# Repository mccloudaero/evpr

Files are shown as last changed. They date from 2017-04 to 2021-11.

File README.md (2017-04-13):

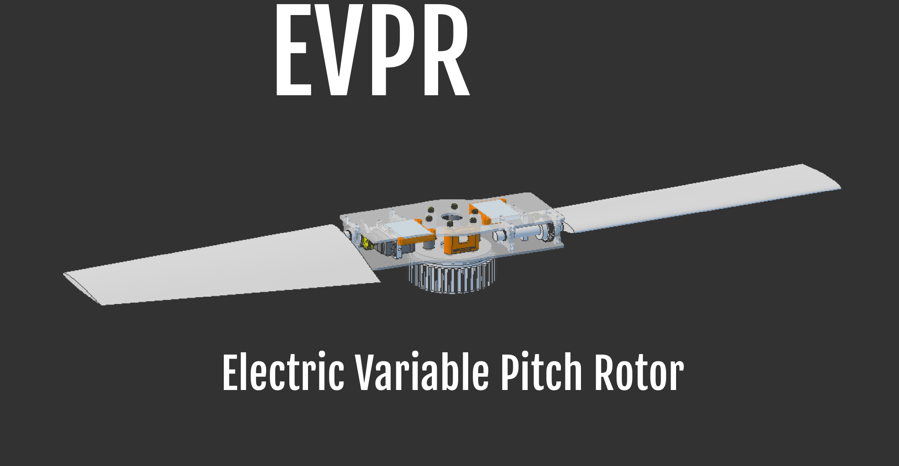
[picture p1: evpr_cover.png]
Cover

# Electric Variable Pitch Rotor (EVPR)
This repository contains the design data for the EVPR designed by
[McCloud Aero Corp](http://www.mccloudaero.com). The primary documentation source can be found at the
[Hackaday Project Page](https://hackaday.io/project/20473-evpr-electric-variable-pitch-rotor)

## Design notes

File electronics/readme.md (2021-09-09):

# Electronics
Electronics design files for EVPR project.

## Contents
* fabrication - Design files for EVPR fabrication processes, including (eventually) full SOPs for each board
* scripts - Scripts used at various points for automating mass alterations to boardfiles
* info - Various human-readable information about the project, including image versions of boardfiles and BOM
* boadfiles - The actual working boardfiles for the EVPR project.

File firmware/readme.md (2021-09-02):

## A summary of the build structure for the absolute newcommer to ESP-IDF:

Firmware for EVPR based on ESP-IDF and ESPNOW

Uses FreeRTOS (as do all ESP-IDF firmware)

ESP-IDF establishes what are known as components. The main folder is a special, hard-coded component that must exist in all ESPIDF projects.

The other components of this project are organized into folders in the components folder. The name of each subfolder of components is the name of the component.

Each component, including main, must contain number of important files. These are described below, but full documentation is available [here](https://docs.espressif.com/projects/esp-idf/en/latest/esp32/api-guides/build-system.html#id3)

CMakeLists.txt is used by the ESP-IDF compilation toolchain, and defines relevant data for the configuration of the component -- mainly the source files, and the components that the given component references. Notably, the main component does not seem to need to specify requirements, but other components must.

Each component may contain an include folder. Only the contents of this folder are made accessible by the linker to components which require the component. Therefore, hfiles for the component typically live here. Note that the include folder must be specified in the CMakeLists.txt for the component, otherwise it is inert.

Kconfig.projbuild allows the specification of preprossessor directive defines that are accessible to the source code in the component which has them. These settings are then modifiable using idf.py menuconfig.

cmake-build-debug sources are auto-generated during the build process and can be ignored. Ideally, they are excluded by the gitignore file.

There are a couple of relevant files that are at the PROJECT level, not the component level. These are the project-level CMakeLists.txt and sdkconfig.

sdkconfig is autogenerated by menuconfig, and it is what actually makes available the various preprocessor defines that are specified in the Kconfig.projbuild files.

The CMakeLists.txt file in the global scope appears to be boilerplate to keep the internal CMake build system happy. Not sure it really accomplishes much of relevance, though.

The build folder is generated during build process and can be ignored. Ideally, it is excluded by the gitignore.

The remainder of the files not yet described should be the actual component source files. They are, of course, source files!

## A summary of the project structure
This firmware implements three distinct node types: head, rotor, and monitor.

Master receives control data from a flight controller and transmits this data over ESPNOW to rotors. Currently, over UART. Later, maybe, over CAN bus.

Rotors receive control data from ESPNOW and execute on it.

Monitors are not implemented yet, but can passively receive rotor data.

Each node type has its own component implementing behavior that is specific to that component.

However, the communications protocol programming is unified and implemented in a single component: ESPComms, which is used by the other components.

The Main component serves only to load in one of the other components based on the configured node type.

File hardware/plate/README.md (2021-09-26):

# Rotor Plates
Both plates have the same outline, but differ in which side the pockets are on and if the PCB mounting holes are present.
Plate one is designed to hold the PCB (4-40 mounting holes).
Plate two is a mirror of plate one, and doesn't have the PCB mounting holes.

For a CCW rotor, plate one is on the bottom. For a CW rotor, plate one is on the top.

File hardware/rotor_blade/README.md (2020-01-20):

# Rotor Blade Info
The rotor blades are made from foam and fiberglass with a carbon-fiber stiffener. The rotor shaft is embedded in the blade and rivets are used to attach the shaft due to the loads and vibration.

# Design Notes
Create profiles and export to txt file, tab delimited
## CAD
* Import txt files, fit as spline
* Set the rotation point at the quarter chord along the chord axis
* Rotate around the quater chord point to the correct angle

# Build Notes
* Tool paths for machining the rotor cores is included in this directory.
	* Cut stock block to 17"x8"x1.75"
* STL file is available for creating your own tool paths

This repository contains the design data for the EVPR designed by
[McCloud Aero Corp](http://www.mccloudaero.com)

Additional documentation at:
[Hackaday Project Page](https://hackaday.io/project/20473-evpr-electric-variable-pitch-rotor)

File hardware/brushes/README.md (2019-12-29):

# Brush Holder
## Assembly
1) Clear the rivet holes using a #30 drill bit
2) Cut power and ground Wires (length TBD)
3) Solder ring terminals onto the wires
4) Run the wires through the central hole in the holder
5) Solder the XT connector onto the wires
6) Place brass rivet using 1/4" key stock
7) Place ring terminal on the rivet and hammer rivet
8) Use liquid tape to insulate ring terminals
9) Sand brushes flat
10) Install brushes, use tape to temporariy hold in place

See the general assembly instructions for the next steps

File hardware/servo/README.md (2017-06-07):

# Servo Sizing for EVPR
The servo needs to be sized according to the intended application. Airfoil selection should consider the section pitching moment. The blade torque needs to be determined by analysis (or testing). Once the required blade torque is known, the gear ratio and the required servo torque can be determined. The figure below shows the required blade torque for the Goliath Quadcopter.

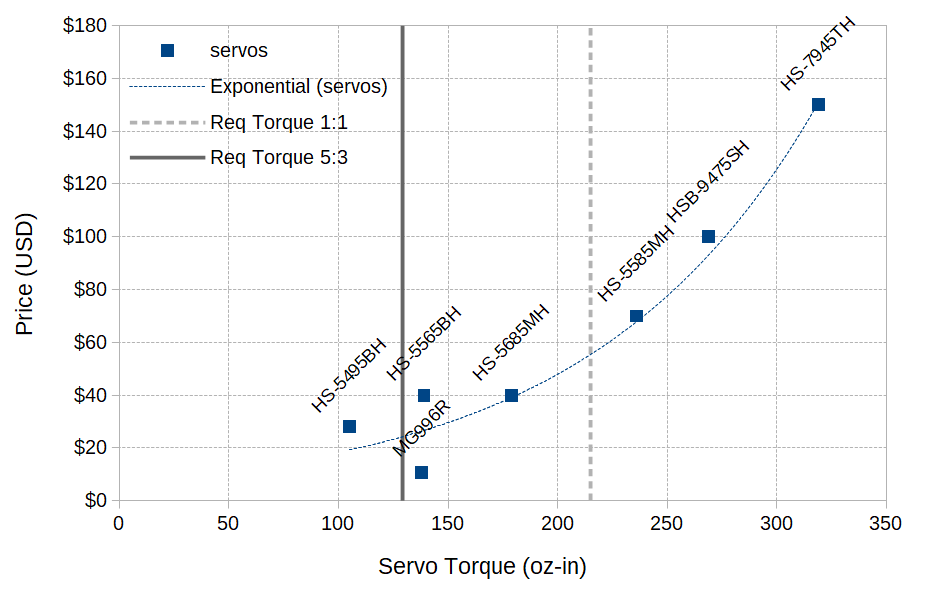
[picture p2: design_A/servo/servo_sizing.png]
Servo Selection


While the HS-5565BH, and MG996R both meet the minimum torque requirement for a gear ratio of 5:3, the HS-5685MH was selected to provide additional margin.  

Additional information can be found at:
[McCloud Aero Corp](http://mccloudaero.com)
[Hackaday Project Page](https://hackaday.io/project/20473-evpr-electric-variable-pitch-rotor)

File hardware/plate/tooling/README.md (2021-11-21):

# Tool Path Setup
* Make sure pockets are on top
* Add 0.25" to the stock in both X and Y
* Cap Larger Holes
* Setup 4-40 holes tool path using drill holes tool.
  * Note that a bug keeps the plung rate at 10 inches per minute
  * Use notepad++ to find/replace F10.0 with F1.0

# Plate One

## 1/16" Bit - 2 Flute, 10,000 RPM
* plate_one_01_4-40_holes_0p0625.nc - 1 minute
* plate_one_02_6-32_holes_0p0625.nc - 2 minutes
## 1/8" Bit - 1 Flute, 10,000 RPM
* plate_one_03_6-32_clearance_holes_0p125.nc - 2 minutes
* plate_one_04_pockets_0p125.nc - 13 minutes
* plate_one_05_remaining_holes_0p125.nc - 8 minutes
## 1/4" Bit - 2 Flute, 9,000 RPM
* plate_one_06_outline_0p25.nc - 20 minutes

# Plate Two

## 1/16" Bit - 2 Flute, 10,000 RPM
* plate_two_01_6-32_holes_0p0625.nc - 12 minutes
## 1/8" Bit - 1 Flute, 10,000 RPM
* plate_one_03_6-32_clearance_holes_0p125.nc - 2 minutes
* plate_one_04_pockets_0p125.nc - 13 minutes

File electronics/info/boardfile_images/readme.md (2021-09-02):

Board Images exported at 1000 pixels per inch
Schematic Images exported at 250 pixels per inch

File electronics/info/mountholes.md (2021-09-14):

## Mounting hole locations in mils relative to the rotor shaft:

```
x		y
-1210		-880
-899    	-1735
570   		-2008
1980    	-840
```

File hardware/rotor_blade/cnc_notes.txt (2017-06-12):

# CNC Notes
Cut stock block to 17"x8"x1.75"

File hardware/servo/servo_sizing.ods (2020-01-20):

Hitec (from Servo City)
Servo | Spline | Torque Min | Torque Max | Price | Gears
HS-5495BH |  | 89 | 105 | $27.99 | Karbonite
HS-5565BH |  | 122 | 139 | $39.99 | Metal | http://hitecrcd.com/products/servos/sport-servos/digital-sport-servos/hs-5565mh-economical-high-speed-digital-coreless-servo-/product
HS-5685MH |  | 157 | 179 | $39.99 | Metal | http://hitecrcd.com/products/servos/sport-servos/digital-sport-servos/hs-5685mh-high-torque-hv-metal-gear-servo-/product
HS-5585MH |  | 194 | 236 | $69.99 | Metal | http://hitecrcd.com/products/servos/sport-servos/digital-sport-servos/hs-5585mh-economical-high-torque-digital-coreless-servo/product
HSB-9475SH |  | 269 | 269 | $99.99 | Steel | http://hitecrcd.com/products/servos/digital-brushless-servos/hsb-9475sh-multi-purpose-brushless-steel-gear-servo/product
HSB-9485SH |  | 361 | 361 | $99.99 | Steel | https://hitecrcd.com/products/servos/digital-brushless-servos/hsb-9485sh-high-torque-brushless-steel-gear-servo/product
HS-7945TH |  | 250 | 319 | $149.99 | Metal
MG996R |  |  | 138 | $10.75
Builda | H25T | 168 | 201 | $24.99 | Metal
Req Torque 1:1
 | 215 | 0
 | 215 | 180
Req Torque 5:3
Servo Gear | 24 | Teeth
Axle Gear | 40 | Teeth
Ratio | 1.67
 | 129 | 0
 | 129 | 180
42 in
Req Torque 1:1 |  | 0.5
4 Blade | 456 |  | 0
4 Blade | 456 |  | 180
Blade A | 412.61 | 816.32 | 0
Blade A | 412.61 |  | 180
Blade C | 440.26 |  | 0
Blade C | 440.26 |  | 180
Req Torque 5:3
Servo Gear | 24 | Teeth | 0.75 | in
Axle Gear | 40 | Teeth | 1.25 | in
Ratio | 1.67 |  | 1
 | 273.6 | 0
 | 273.6 | 180
Req Torque 3:1
Servo Gear | 16 | Teeth | 0.5 | in
Axle Gear | 48 | Teeth | 1.5 | in
Ratio | 3 |  | 1
 | 152 | 0
 | 152 | 180

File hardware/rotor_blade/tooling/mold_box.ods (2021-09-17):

Box Dimensions |  | AM125
17.375 | in | specific gravity | 1.34
6.125 | in | Required Weight | 114.820689797297 | oz
1.75 | in |  | 7.17629311233106 | lbs
Box Volume |  | AM128
186.24 | in3 | specific gravity | 1.25
103.20 | fluid oz | Required Weight | 107.108852422852 | oz
 |  |  | 6.69430327642822 | lbs
Part Volume
31.6 | in3
Mold Volume
154.63828125 | in3
85.69 | fluid oz

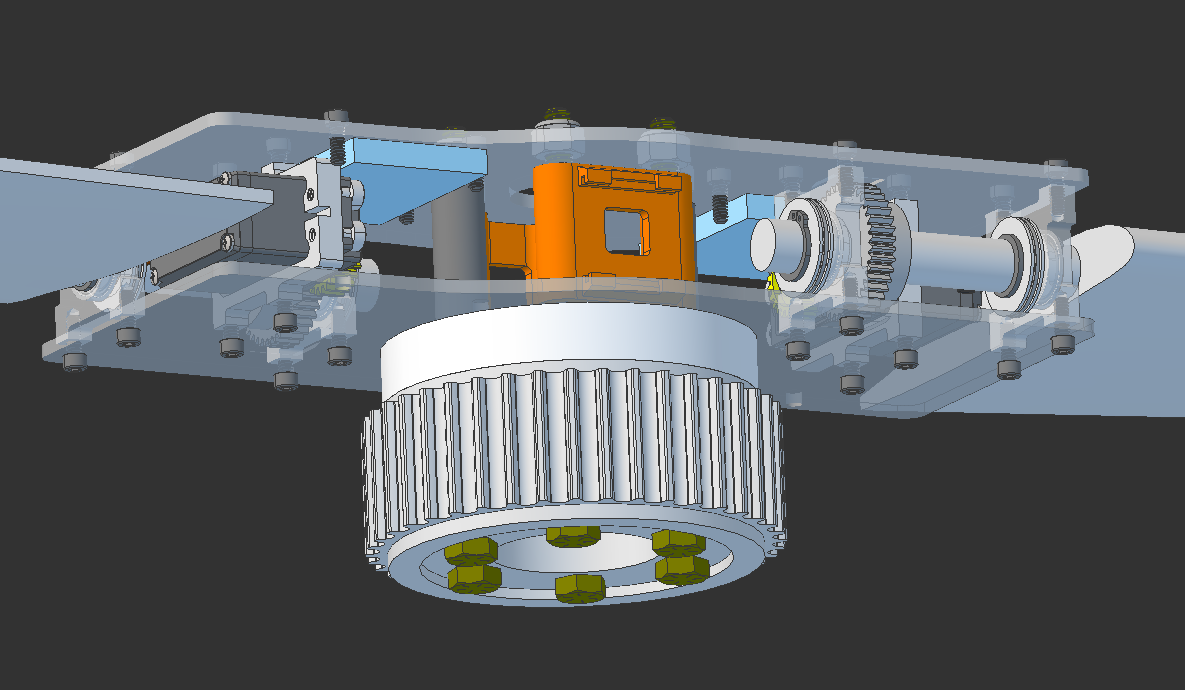
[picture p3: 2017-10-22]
hardware/hub_batteries.png

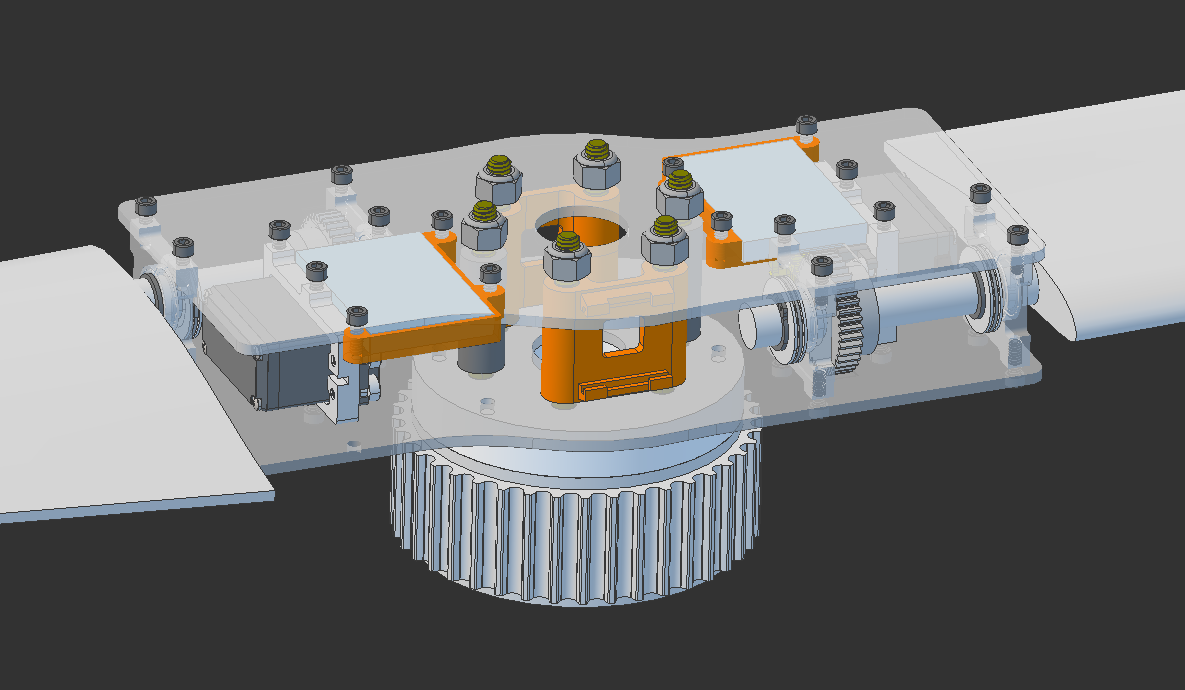
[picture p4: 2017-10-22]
hardware/hub_closeup_iso.png

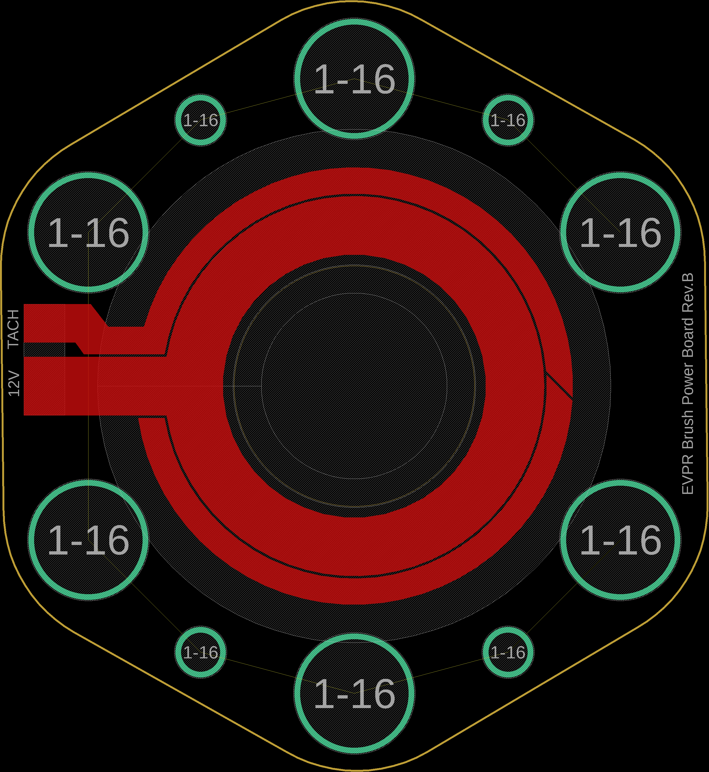
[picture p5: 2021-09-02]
electronics/info/boardfile_images/brush_top.png

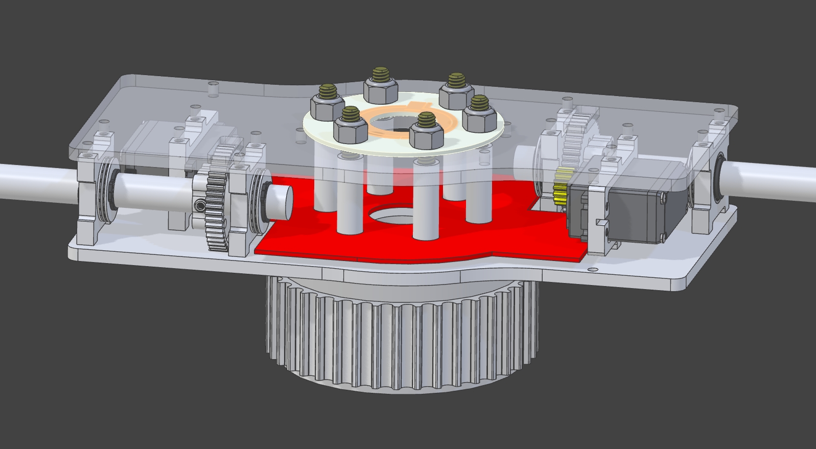
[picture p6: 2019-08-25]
hardware/hub_ccw.png

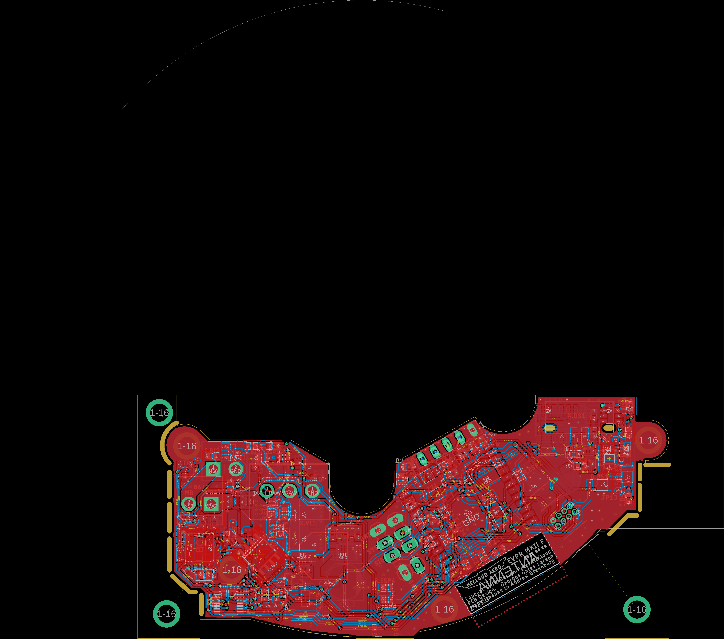
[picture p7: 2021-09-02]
electronics/info/boardfile_images/mainboard_bot_top.png

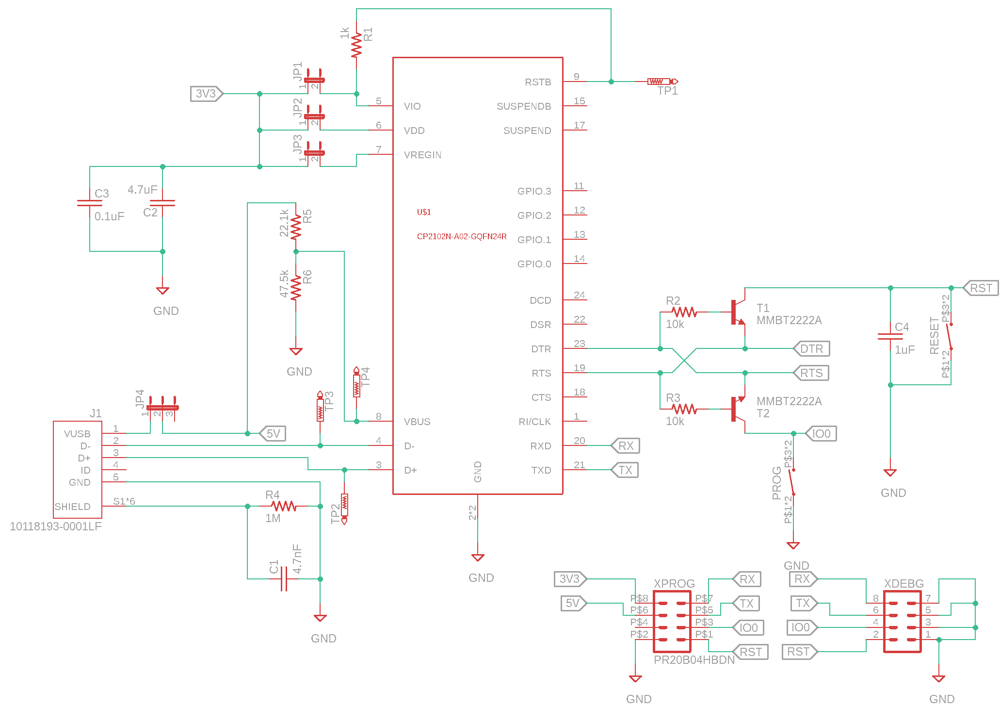
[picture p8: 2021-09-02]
electronics/info/boardfile_images/programmer_sch.png

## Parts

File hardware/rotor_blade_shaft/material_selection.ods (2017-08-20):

Diameter | 0.5 | inch
Area | 0.1963495408 | inch2
Material | Yield (psi) | Axial Force (lbs) | Cost/ft
Al 7075 | 73,000 | 14,334 | $10.78
Al 6061 | 35,000 | 6,872 | $21.49
Al 2024 | 37,000 | 7,265 | $13.32
Steel 1035 | 75,000 | 14,726 | $10.20
5/32 | 0.15625
3/32 | 0.09375
3/16 | 0.1875
'9/32 | 0.28125

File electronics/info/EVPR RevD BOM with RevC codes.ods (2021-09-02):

Rev3 Component | Rev3 Top | Rev3 Bot | Group | Quant. Per Unit. | Min for 5 | Available? | Available When? | Salvageable? | Replaceable? | Unit Cost | Cost per EVPR
06033C104JAT2A Cheaper (NOT! EXPENSIVE SHIPPING FEE!): GMC10X7R104J25NT | ['C.BI1', 'C.BI2', 'C.DS5', 'C.DS9', 'C.DS10', 'C.DS11', 'C.ESP1', 'C.SI1', 'C.ZZ3', 'C.ZZ5', 'C.ZZ6'] | ['C.BC1', 'C.BC2', 'C.DS3', 'C.EC7', 'C.VI1', 'C.VI3', 'C.YY1', 'C.YY4'] | C.B | 19 | 95 | Yes | Now | Yes | Yes | 0.1574 | 2.9906
875075355002 | ['C.EC6'] | [] | C.C | 1 | 5 | Yes | Now | Probably | Probably | 0.95 | 0.95
AP63203WU-7 | ['U.ZZ1'] | [] | U.D | 1 | 5 | No | Never | Yes | No | 0.87 | 0.87
AP63205WU-7 | [] | ['U.DS2'] | U.E | 1 | 5 | No | Never | Yes | No | 0.87 | 0.87
APXG250ARA560MF61G OR: 25SVPF56M | [] | ['C.EC3', 'C.EC4'] | C.F | 2 | 10 | Yes | Now | Probably | Yes | 1.022 | 2.044
B2P-VH(LF)(SN) | [] | [] |  | 2 | 10 | No | Never | Maybe | Maybe | 0.179 | 0.358
B3P-VH(LF)(SN) | [] | [] |  | 1 | 5 | No | Never | Maybe | Maybe | 0.24 | 0.24
BM02B-PASS-1-TFT(LF)(SN) | ['X.SI1'] | [] |  | 1 | 5 | No |  | Probably | Unlikely | 0.66 | 0.66
BM03B-PASS-1-TFT(LF)(SN) | ['X.SI2'] | ['X.SI3'] |  | 2 | 10 | No | Never | Probably | Unlikely | 0.73 | 1.46
BM04B-PASS-1-TFT(LF)(SN) | ['X.DS1'] | [] |  | 1 | 5 | No | Never | Probably | Unlikely | 0.78 | 0.78
BSS84-7-F | ['Q.BI1'] | ['Q.BI2'] | Q.G | 2 | 10 | No | Never | Yes | Yes | 0.207 | 0.414
C0603C474K4PACTU | ['C.BC5'] | [] | C.H | 1 | 5 | Yes | Now | Yes | Yes | 0.15 | 0.15
C1Q 1 | ['F.DS1'] | [] | F.I | 1 | 5 | Yes | Now | Yes | Probably | 0.3 | 0.3
C3225X7R1E106K250AC | [] | ['C.EC1', 'C.EC2'] | C.J | 2 | 10 | No | Never | Yes | Unlikely | 0.49 | 0.98
CL10A226MO7JZNC | ['C.ZZ1', 'C.ZZ4'] | ['C.BC3', 'C.BC4', 'C.DS6', 'C.DS8'] | C.L | 6 | 30 | No | Never | Yes | No | 0.477 | 2.862
CL10B562KB8NNNC | [] | ['C.YY2', 'C.YY3'] | C.O | 2 | 10 | Yes | Now | Yes | Yes | 0.037 | 0.074
CL32A476KOJNNNE | [] | ['C.EC5'] | C.P | 1 | 5 | Yes | Now | Yes | Probably | 0.82 | 0.82
CSD88537NDT | ['Q.YY2'] | [] | Q.R | 1 | 5 | Yes | Never | Yes | Unlikely | 1.58 | 1.58
CSR0603FKR250 | [] | ['R.BC3'] | R.S | 1 | 5 | No | Never | Yes | Probably | 0.36 | 0.36
DMN5L06K-7 | ['Q.ZZ4', 'Q.ZZ5'] | [] | Q.T | 2 | 10 | No | Never | Yes | Yes | 0.352 | 0.704
ESP32-WROOM-32E | [] | ['U.ESP1'] | U.U | 1 | 5 | No | Never | Unlikely | No | 3.6 | 3.6
GRM188R61E106MA73J (https://www.digikey.com/en/products/detail/murata-electronics/GRM188R61E106MA73J/4905347) | ['C.ZZ2'] | ['C.DS7'] | C.V | 2 | 10 | No | Now | Yes | Yes | 0.246 | 0.492
LTC4353CMS#PBF | ['U.YY1'] | [] | U.W | 1 | 5 | No | Never | Probably | No | 8.27 | 8.27
LTST-C171GKT OR 150080GS75000 | ['D.USB1', 'D.VI1', 'D.ZZ1'] | [] | D.X | 3 | 15 | Yes | Now | Yes | Yes | 0.18 | 0.54
MP2615 | [] | ['U.BC1'] | U.Z | 1 | 5 | Yes | Now | Yes | No | 2.85 | 2.85
RC0603FR-0737K4L OR: ERJ-3EKF37R4V | [] | ['R.EC2'] | R.BB | 1 | 5 | Yes | Now | Yes | Yes | 0.1 | 0.1
RG1608P-103-B-T5 | ['R.EC1'] | [] | R.CC | 1 | 5 | No | Never | Yes | Yes | 0.36 | 0.36
RMCF0603FT100K | ['R.ESP3', 'R.ESP4', 'R.YY2', 'R.ZZ2', 'R.ZZ3'] | ['R.BC1', 'R.BC2', 'R.VI2', 'R.VI4'] | R.EE | 9 | 45 | Yes | Now | Yes | Yes | 0.017 | 0.153
RMCF0603FT10K0 | ['R.ESP2'] | [] | R.FF | 1 | 5 | No | Never | Yes | Yes | 0.1 | 0.1
RMCF0603FT1K00 | ['R.VI1'] | [] | R.GG | 1 | 5 | Yes | Now | Yes | Yes | 0.1 | 0.1
RMCF0603JT22K0, RMCF0603FT22K1 | ['R.BI4', 'R.YY1'] | ['R.BI2', 'R.VI3', 'R.VI5'] | R.HH | 5 | 25 | Yes | Now | Yes | Yes | 0.017 | 0.085
RMCF0603FT47K5 | ['R.BI3'] | ['R.BI1'] | R.II | 2 | 10 | Yes | Now | Yes | Yes | 0.017 | 0.034
RMCF0603FT95K3 | ['R.EC4'] | [] | R.JJ | 1 | 5 | Yes | Now | Yes | Yes | 0.1 | 0.1
RMCF0603JT300R | ['R.USB4', 'R.ZZ1'] | [] | R.KK | 2 | 10 | Yes | Now | Yes | Yes | 0.015 | 0.03
RQ73C1J768RBTD | ['R.EC3'] | [] | R.LL | 1 | 5 | Yes | Now | Yes | Yes | 0.79 | 0.79
SI7997DP | [] | ['Q.YY1'] | Q.MM | 1 | 5 | No | Never | Yes | No | 2.3 | 2.3
SMD34LHE1-TP | ['Q.DS1', 'Q.DS2', 'Q.ZZ1', 'Q.ZZ2', 'Q.ZZ3'] | [] | Q.OO | 5 | 25 | Yes | Now | Yes | Probably | 0.322 | 1.61
SN74AHCT125DR | [] | ['U.DS1'] | U.PP | 1 | 5 | Yes | Now | Yes | Yes | 0.47 | 0.47
SRN5040TA-330M OR: SRN5040TA-101K | ['L.BC1'] | [] | L.QQ | 1 | 5 | No | Never | Probably | Unlikely | 0.6 | 0.6
SRR4818A-3R9Y | ['L.ZZ1'] | ['L.DS1'] | L.RR | 2 | 10 | No | Never | Probably | Maybe | 1.02 | 2.04
TPSM84824MOLR | [] | ['U.EC1'] | U.SS | 1 | 5 | No | Never | Yes | No | 11.69 | 11.69
UWT0J102MNL1GS | [] | ['C.DS1'] | C.TT | 1 | 5 | No | Never | Probably | Probably | 0.58 | 0.58
VESD16A2-03G-G3-08 | [] | ['Q.VI1'] | Q.UU | 1 | 5 | No | Never | Yes | Probably | 0.4 | 0.4
CR0603-J/-000ELF | ['R.SI1*', 'R.SI2*', "R.DS2*'] | ['R.DS1*'] | R.VV | 4 | 20 | Yes | Now | Yes | Yes | 0.013 | 0.052
Amtech Syntech Solder Paste |  |  |  | 0.07 |  | Yes | Now | No | No | 33.99 | 2.266

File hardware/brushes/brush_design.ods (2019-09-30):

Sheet: Brush Speed
Brush Design
http://www.argointl.com/wp-content/uploads/2014/03/necp-How_to_Select_Brushes_for_Motors_and_Generators2.pdf
Nominal RPM | 3600 |  | 376.99 | rad/s
Brush Radius | 0.86 | in | 0.0219 | m
Brush Speed | 1624.83 | ft/min | 8.2541 | m/s
 | 4000 | Carbon Graphite
 | 7000 | Electrographitic
Length | Width | Area | A/in | Amps
0.25 | 0.25 | 0.0625 | 80 | 5
0.5 | 0.25 | 0.125 | 80 | 10
0.5 | 0.5 | 0.25 | 80 | 20

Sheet: Morgan Grades
Morgan
Type | Grade | Contact Drop | Friction | Speed | Current Density
Electrographitic | 258 | H | L | 6000 | 80
Electrographitic | B344 | H | M | 6000 | 80
Electrographitic | D | H | L | 6000 | 80
Graphite | K816 | M | M | 8000 | 65
Graphite | R318 | H | M | 10000 | 65
Graphite | K816 | H | M | 12000 | 65
Metal Graphite | AJT | L | L | 6000 | 100
Metal Graphite | ANK | L | L | 6000 | 150
Metal Graphite | AYK | M | M | 4000 | 100
Metal Graphite | L4 | L | H | 5000 | 125

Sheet: Helwig Carbon ElectroGraphite
Grade | Shunt? | Spring? | OHM-IN | µOHM-M | Shore | PSI | N/mm2 | VD | CF | Film# | Amp/in2 | Amp/cm2 | Metal %
H76 | Yes | Yes | 0.003 | 75 | 65 | 2400 | 16.6 | H | L | 3 | 80 | 12.4 | 40

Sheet: Helwig Carbon Copper Graphite
Grade | Shunt? | Spring? | OHM-IN | µOHM-M | Shore | PSI | N/mm2 | VD | CF | Film# | Amp/in2 | Amp/cm2 | Metal %
6H2 | Yes | No | 0.00012 | 3 | 30 | 3700 | 25.5 | L | L | 1 | 110 | 17.1 | 40
6H3 | Yes | No | 6E-05 | 1.8 | 25 | 3200 | 22.1 | L | L | 1 | 120 | 18.6 | 50
6H7 | Yes | No | 3.3E-05 | 0.64 | 25 | 3400 | 23.4 | L | L | 1 | 130 | 20.2 | 65
6H8 | Yes | No | 1.3E-05 | 0.33 | 22 | 4500 | 31 | VL | L | 1 | 140 | 21.7 | 75
H670 |  |  | 0.00018 | 4.5 | 40 | 5100 | 35.2 | L | L | 2 | 110 | 17.1 | 40
H671 |  |  | 0.00025 | 6.3 | 50 | 6000 | 41.3 | L | M | 1 | 110 | 17.1 | 30
H680 |  |  | 3.2E-06 | 0.08 | 18 | 9300 | 64.1 | L | L | 1 | 150 | 23.3 | 87
H682 |  |  | 5E-06 | 0.13 | 25 | 5100 | 35.2 | L | VL | 1 | 140 | 21.7 | 75
H692 |  |  | 2.7E-06 | 0.07 | 18 | 8800 | 60.7 | VL | L | 1 | 160 | 24.8 | 90
H693 |  |  | 2.4E-06 | 0.06 | 20 | 11500 | 80 | VL | L | 1 | 175 | 27.1 | 95
H4333 |  |  | 0.00015 | 3 | 23 | 4000 | 27.5 | VL | L | 2 | 130 | 20.2 | 40
H4375 |  |  | 0.0003 | 6.6 | 23 | 3000 | 20.7 | VL | L | 2 | 110 | 17.1 | 30
K076 | Yes | No | 2E-05 | 0.5 | 13 | 13000 | 89.6 | VL | L | 1 | 175 | 27.1 | 91
K086 | Yes | No | 2E-06 | 0.05 | 7 | 9000 | 62.1 | VL | L | 1 | 160 | 24.8 | 91
K106 | Yes | No | 4E-06 | 0.1 | 8 | 6150 | 42.4 | VL | L | 1 | 150 | 23.3 | 85
K107 |  |  | 3E-06 | 0.08 | 25 | 6500 | 44.8 | VL | L | 2 | 130 | 20.2 | 59
K136 | Yes | Yes | 1.3E-05 | 0.33 | 18 | 4800 | 33.1 | VL | L | 1 | 140 | 21.7 | 75
K165 |  |  | 0.0003 | 6.6 | 25 | 2500 | 17.2 | L | L | 2 | 110 | 17.1 | 43
K175 |  |  | 0.00016 | 4.06 | 45 | 5000 | 34.4 | L | L | 2 | 110 | 17.1 | 40
K176 | Yes | Yes | 3.3E-05 | 8.4 | 25 | 5000 | 34.4 | L | L | 1 | 130 | 20.2 | 65
K216 |  |  | 0.0001 | 2.54 | 20 | 4000 | 27.5 | L | L | 1 | 140 | 21.7 | 77.5
K236 |  |  | 2E-05 | 0.5 | 20 | 9000 | 62.1 | L | VL | 1 | 150 | 23.3 | 85

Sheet: Helwig Parts
https://www.helwigcarbon.com/resources/grade-information/
Carbon/Graphite
Part # | Grade | VD | CF | Thickness (in) | Width (in) | Length (in) | Area (in2) | Amps/In2 | Capacity (amps) | Cost ($)
10-121871
10-122521 | H27 |  |  | 0.125 | 0.25 | 0.625 | 0.031 | 80 | 2.50 | $6.08 | https://www.helwigcarbon.com/shop/10-122521/ | 0
10-151511 | H22 |  |  | 0.152 | 0.152 | 0.625 | 0.023 | 70 | 1.62 | $4.95 | https://www.helwigcarbon.com/shop/10-151511/ | 0
10-181811 | H3 |  |  | 0.187 | 0.187 | 0.625 | 0.035 | 70 | 2.45 | $4.95 | https://www.helwigcarbon.com/shop/10-181811/ | 0
30-151111 | H3 |  |  | 0.157 | 0.118 | 0.394 | 0.019 | 70 | 1.30 | $4.95 | https://www.helwigcarbon.com/shop/30-151111/
10-252523 | H27 | H | VL | 0.252 | 0.252 | 0.625 | 0.064 | 80 | 5.08 | $5.30 | https://www.helwigcarbon.com/shop/10-252523/ | 1
213 | H76 | H | L | 0.25 | 0.25 | 0.625 | 0.063 | 80 | 5.00 | $5.12 | https://www.helwigcarbon.com/shop/213/ | 1
279 | H76 | H | L | 0.25 | 0.25 | 0.593 | 0.063 | 80 | 5.00 | $5.30 | https://www.helwigcarbon.com/shop/279/ | 1
35-313121 | H22 | M | L | 0.311 | 0.311 | 0.622 | 0.097 | 70 | 6.77 | $6.10 | https://www.helwigcarbon.com/shop/35-313121 | 1
393 | H38 | M | VL | 0.25 | 0.25 | 0.562 | 0.063 | 80 | 5.00 | $5.30 | https://www.helwigcarbon.com/shop/393/ | 1
404 | H76 | H | L | 0.25 | 0.25 | 0.593 | 0.063 | 80 | 5.00 | $5.30 | https://www.helwigcarbon.com/shop/404-carbon-brush/ | 1
425 | H76 | H | L | 0.25 | 0.25 | 0.5 | 0.063 | 80 | 5.00 | $5.26 | https://www.helwigcarbon.com/shop/425/ | 1
482 | H76 | H | L | 0.25 | 0.375 | 0.5 | 0.094 | 80 | 7.50 | $6.02 | https://www.helwigcarbon.com/shop/482/
Copper Graphite
Part # | Grade |  |  | Thickness (in) | Width (in) | Length (in) | Area (in2) | Amps/In2 | Capacity (amps) | Cost ($)
99-362361 | K136 | VL | L | 0.362 | 0.232 | 0.8125 | 0.084 | 140 | 11.76 | $6.51 |  | 1
11-313761 | K136 |  |  | 0.312 | 0.375 | 0.75 | 0.117 | 140 | 16.38 | $7.49 |  | 1
38-272761 | K176 |  |  | 0.275 | 0.275 | 0.75 | 0.076 | 130 | 9.83 | $6.05 | https://www.helwigcarbon.com/shop/38-272761/ | 1
Silver Graphite
Part # | Grade |  |  | Thickness (in) | Width (in) | Length (in) | Area (in2) | Amps/In2 | Capacity (amps) | Cost ($)
13-121871 | K017 |  |  | 0.125 | 0.187 | 0.625 | 0.023 | 140 | 3.27 | $20.57 | https://www.helwigcarbon.com/shop/13-121871/ | 0
25-122471 | K017 |  |  | 0.124 | 0.249 | 0.442 | 0.031 | 140 | 4.32 | $20.57 | https://www.helwigcarbon.com/shop/25-122471/ | 1
30-111571 | K047 |  |  | 0.118 | 0.158 | 0.468 | 0.019 | 100 | 1.86 | $18.85 | https://www.helwigcarbon.com/shop/30-111571/ | 0
92-111571 | K047 |  |  | 0.118 | 0.157 | 0.5 | 0.019 | 100 | 1.85 | $18.85
10-121871 | K057 |  |  | 0.125 | 0.187 | 0.437 | 0.023 | 160 | 3.74 | $24.00 | https://www.helwigcarbon.com/shop/10-121871/

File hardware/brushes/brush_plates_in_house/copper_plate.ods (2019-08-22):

 |  | Cost | 6x6 pieces | Cost per 6x6”
PC 10-S | 6 X 6" | $7.56 | 1 | $7.56
PC 11-T | 12 X 12" | $21.12 | 4 | $5.28
PC 12 | 12 X 18" | $31.67 | 6 | $5.28
PC 12-E | 18 X 18" | $40.56 | 9 | $4.51 | Not sold Anymore
PC 12-1 | 24 X 36" | $89.46 | 24 | $3.73 | Not sold Anymore
PC 12-2 | 36 X 48" | $125.24 | 48 | $2.61 | Not sold Anymore

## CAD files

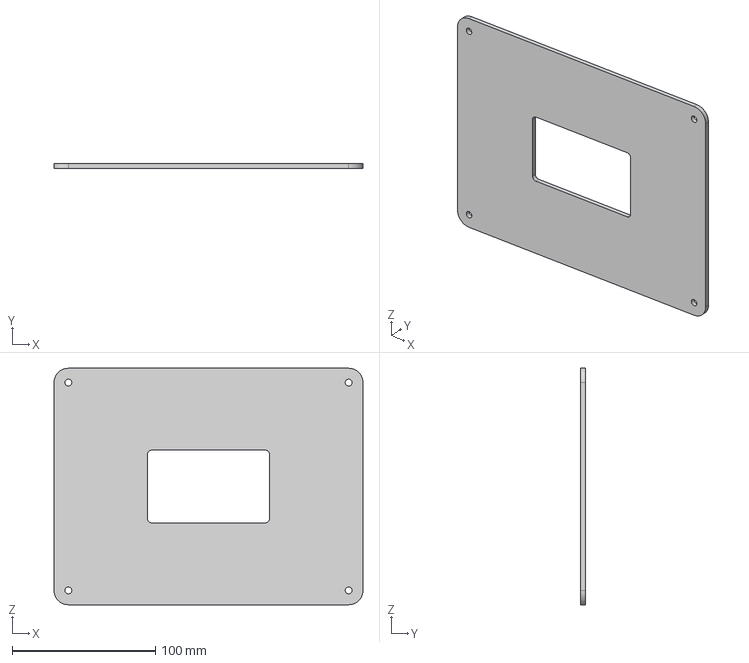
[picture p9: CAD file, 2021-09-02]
electronics/fabrication/pasting platform/paster.step
215.5 x 3.20 x 165.0 mm

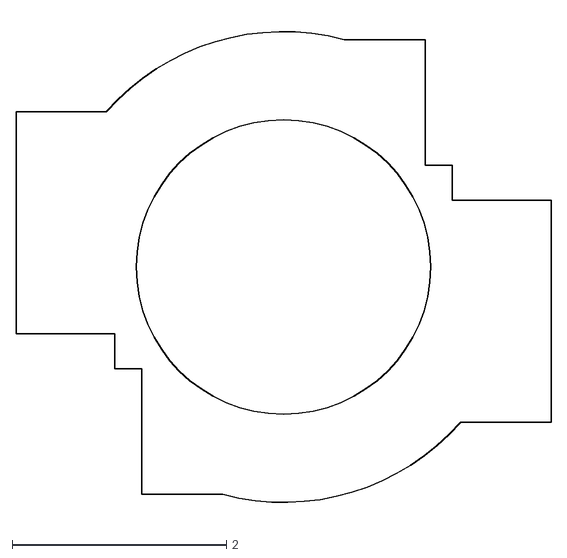
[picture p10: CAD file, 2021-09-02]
electronics/info/footprint/available_foot_print_in.dxf
5.00 x 4.68

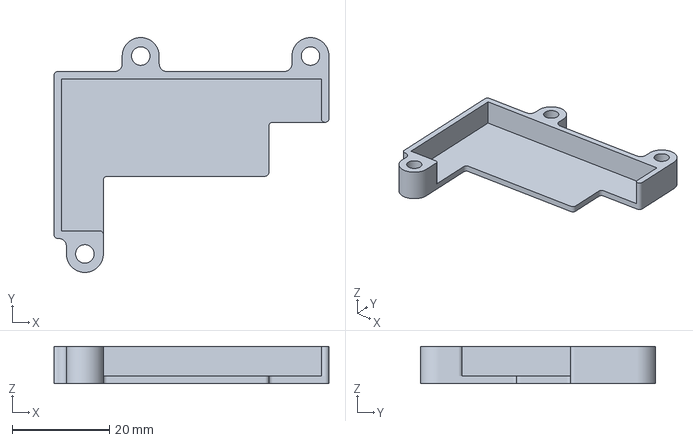
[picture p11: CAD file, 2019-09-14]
hardware/battery/battery_holder.curaproject.3mf
56.6 x 48.3 x 7.62 mm

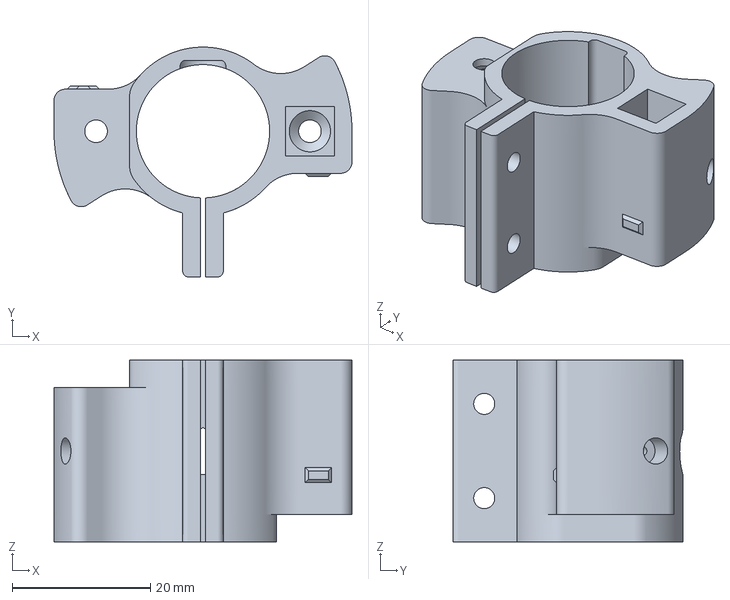
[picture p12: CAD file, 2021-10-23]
hardware/brushes/brush_holder_mm.3mf
43.2 x 33.3 x 26.4 mm

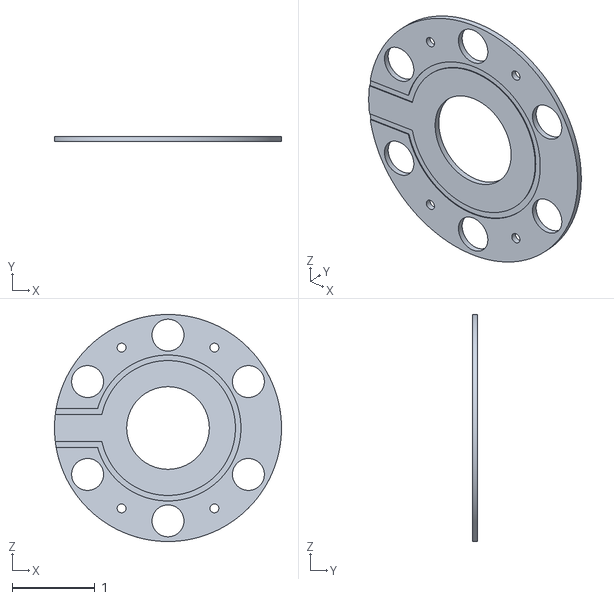
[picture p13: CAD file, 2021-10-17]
hardware/brushes/brush_plates_in_house/brush_plate_power_in.stl
2.75 x 0.0625 x 2.75

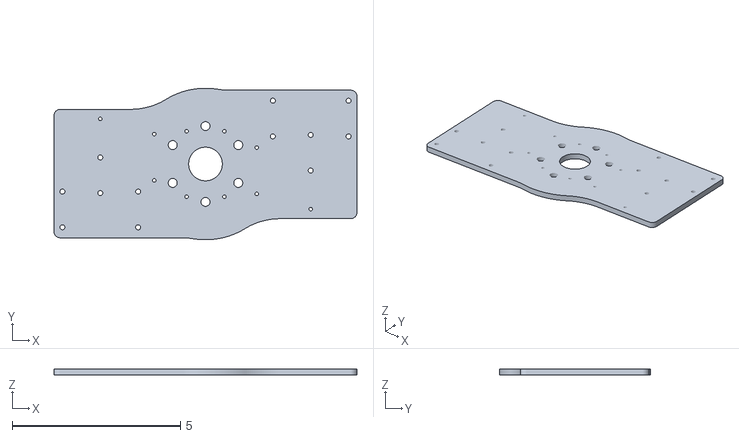
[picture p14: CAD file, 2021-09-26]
hardware/plate/tooling/plate_two_in.stl
9.00 x 4.50 x 0.19

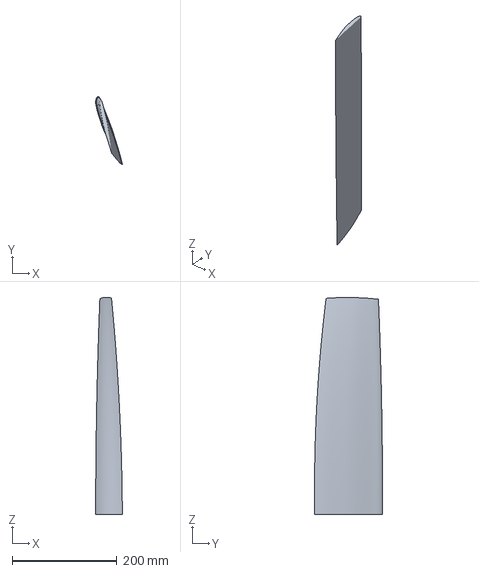
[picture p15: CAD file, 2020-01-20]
hardware/rotor_blade/rotor_blade_ccw_42_dia_D_blade.3mf
50.9 x 129.6 x 413.8 mm

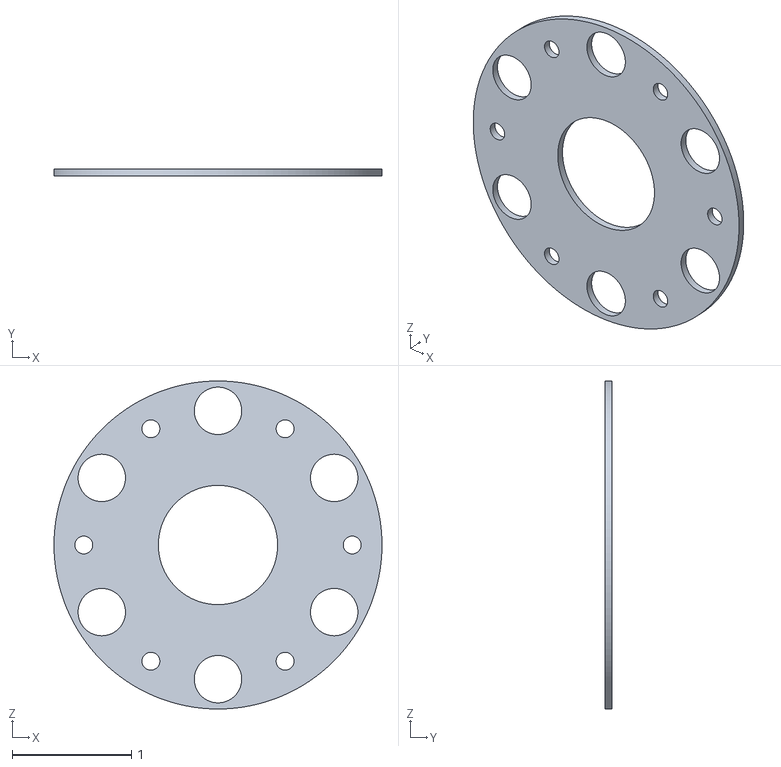
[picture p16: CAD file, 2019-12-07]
hardware/brushes/brush_plates_in_house/brush_plate_ground_in.stl
2.75 x 0.0625 x 2.75

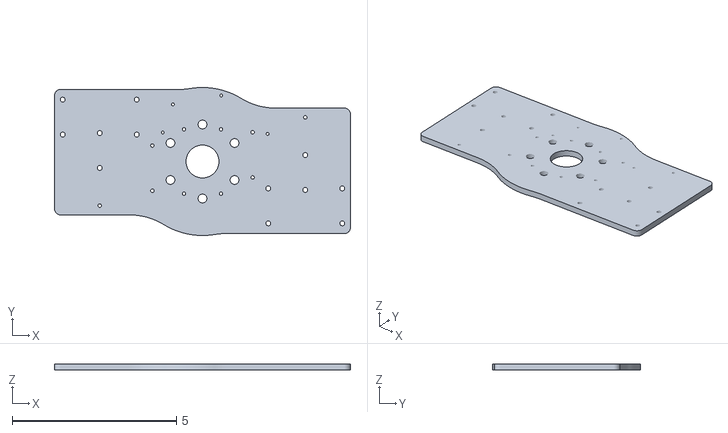
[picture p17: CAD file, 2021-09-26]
hardware/plate/tooling/plate_one_in.stl
9.00 x 4.50 x 0.19

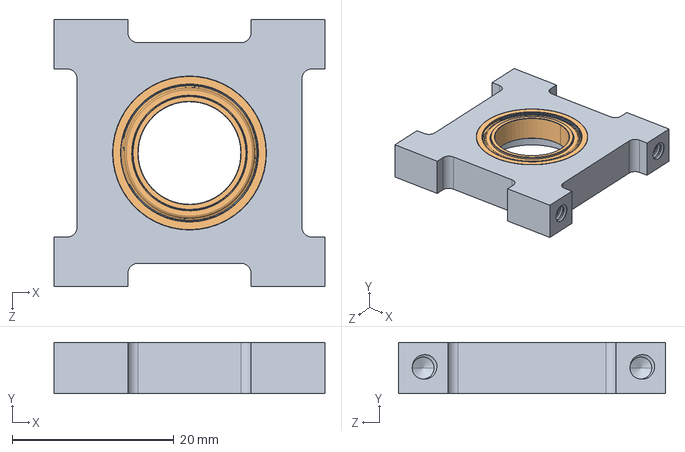
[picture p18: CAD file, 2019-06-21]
hardware/pillow_block/535138 assembly.STEP
33.5 x 6.36 x 33.0 mm

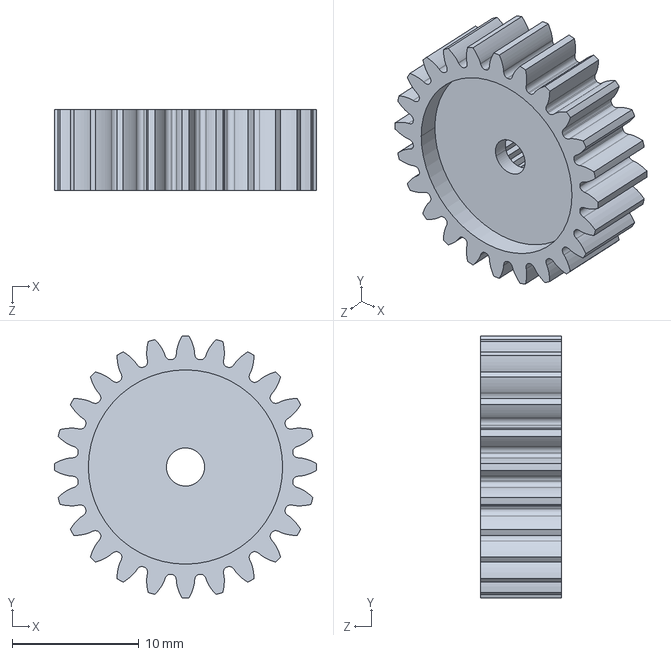
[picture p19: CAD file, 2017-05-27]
hardware/gears/615286.STEP
20.6 x 20.6 x 6.35 mm

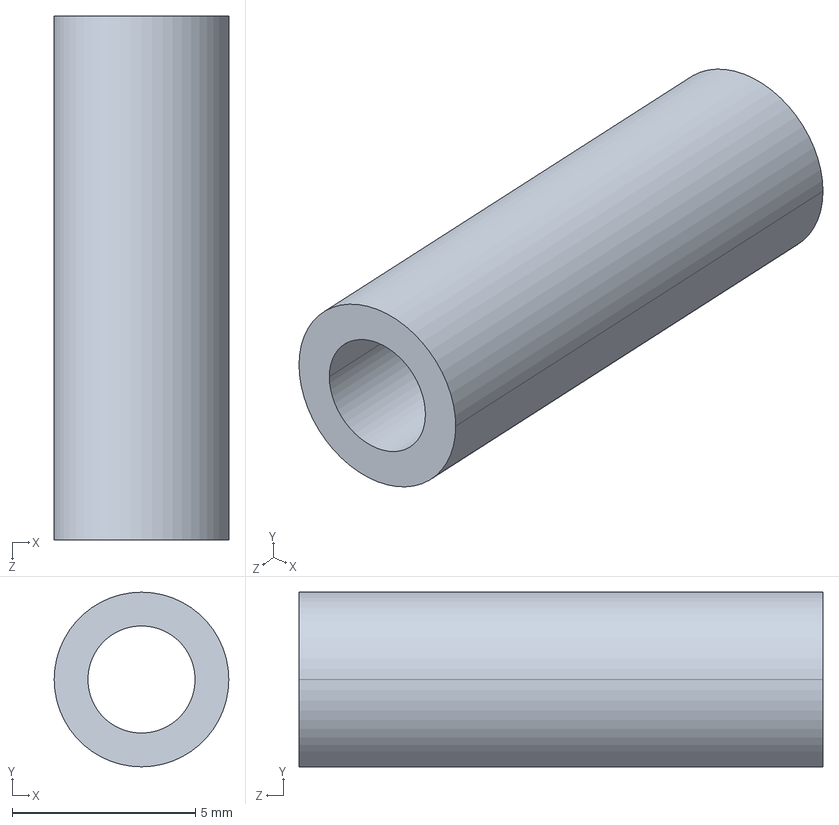
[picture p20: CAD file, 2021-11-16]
hardware/misc/92510A018_unthreaded_spacer.stp
4.76 x 4.76 x 14.3 mm

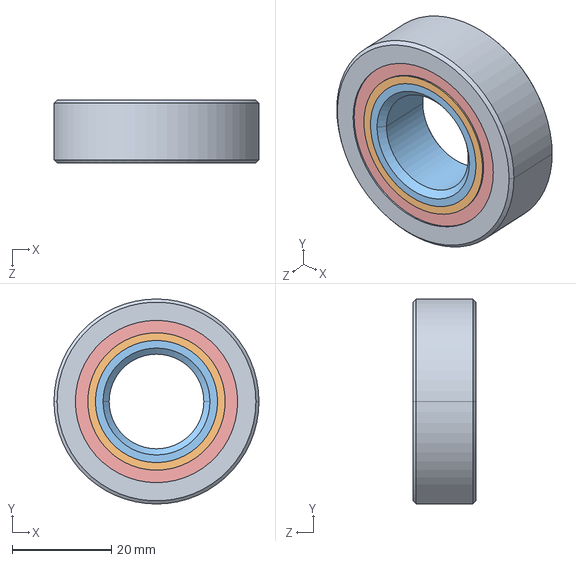
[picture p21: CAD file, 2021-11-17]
hardware/pulley_shaft/bearing/2780T43.STEP
41.3 x 41.3 x 12.7 mm

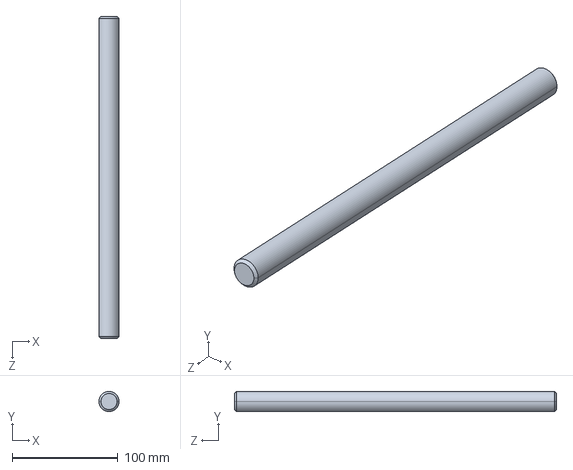
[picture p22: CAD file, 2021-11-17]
hardware/pulley_shaft/shaft/5947K150.STEP
19.0 x 19.0 x 304.8 mm

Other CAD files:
hardware/battery/battery_holder.stl
hardware/battery/battery_holder_ccw.stl
hardware/pulley_shaft/shaft/96363A578.STEP
electronics/fabrication/pasting platform/paster.stl
hardware/brushes/brush_holder_mm.stl

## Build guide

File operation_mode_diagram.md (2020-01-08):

# EVPR Operation/Mode Diagram
Authors Note: The mode diagram was created using mermaid with the hopes that someday Github might support it. You can view currently using https://github.com/BackMarket/github-mermaid-extension. 

```mermaid
graph TB;
  %% Subgraph interconnections
  hard_process2[Power On ESP]-->soft_process1[Boot]
  soft_process1[Boot]-->dotstar[Dotstar]
  decision1{Master Node Found?}--Yes-->process3A[Connected]
  process3A[Connected]-->dotstar[Dotstar]
  decision2{Vehicle Power Available?}--No-->shutdown[SHUTDOWN]
  decision3{Vehicle Power Available?}--No-->shutdown[SHUTDOWN]
  decision5{Armed?}--Yes-->armed1[Armed]
  armed2[Disable Reset]-->rst_disable(RST_DISABLE)
  armed3[Disable Shutdown]-->shutdown_cancel[SHUTDOWN_CANCEL]
  decision6{Armed?}--No-->process3A[Connected]
  
  subgraph Hardware
  vraw(VRAW)-->hard_process1[Detect Rising Edge]
  hard_process1[Detect Rising Edge]-->hard_process2[Power On ESP]
  shutdown[SHUTDOWN]
  dotstar(Dotstar)
  rst_disable(RST_DISABLE)
  shutdown_cancel[SHUTDOWN_CANCEL]
  end

  subgraph Software_Start
  soft_process1[Boot]-->soft_process2[Search for Master Node]
  soft_process2[Search for Master Node]-->decision1{Master Node Found?}
  decision1{Master Node Found?}--No-->decision2{Vehicle Power Available?}
  decision2{Vehicle Power Available?}--Yes-->soft_process2[Search for Master Node]
  end

  subgraph Software_Connected
  process3A[Connected]-->decision3{Vehicle Power Available?}
  decision3{Vehicle Power Available?}--Yes-->decision4{Batteries Ok?}
  decision4{Batteries Ok?}--Yes-->decision5{Armed?}
  end
  
  subgraph Software_Armed
  armed1[Armed]-->armed2[Disable Reset]
  armed2[Disable Reset]-->armed3[Disable Shutdown]
  armed3[Disable Shutdown]-->armed4[Servo Loop]
  armed4[Servo Loop]-->decision6{Armed?}
  decision6{Armed?}--Yes-->armed1[Armed]
  end
 
```

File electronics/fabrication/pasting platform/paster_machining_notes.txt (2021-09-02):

CAD->CAM
Stock 8.7350" x 6.7450"
1. Setup, Rough Holes (End Mill)
	* Add bit width to sides of stock (0.125")
    * Set retract height (0.1")
	* Set circular machining regions to machine holes only
	* Leave 0.02, Depth 0.03125, Stepover 0.03125, Feed 5 IPM, Plunge 2.0 IPM
	* Set "Climb"
2. Finish Holes (End MIll)
	* Pencil, Feed 4 IPM, Plunge 1.5 IPM
3. Rough Remaiing 3 (End Mill)
    * Set Retract Height to 0.5"
	* Clear Machining Regions
	* Exclude Holes
	* Leave 0.00, Depth 0.25, Stepover 0.03125, Feed 7 IPM, Plunge 2.0 IPM

Step 1 - Rough Holes, 0:XX:00, Feed 5 IPM, Plunge 2 IPM
Step 2 - Pencil Holes, 0:XX:00, Feed 5 IPM, Plunge 2 IPM

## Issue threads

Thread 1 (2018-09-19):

New Integrated Electronics

petermccloud, 2018-09-19:
Electronics currently consist of an [Adafruit Huzzah32](https://www.adafruit.com/product/3405) and a custom power distribution board that takes the 7.4V from the (2) 3.7V LiPo batteries and provides power to the servos and the Huzzah32.

Need to design a custom integrated board to replace everything. Min requirements are:

1. ESP32 module
2. USB Port for charging and flashing
3. Power handling and charging for the 2 LiPos

Flynnn, 2019-06-16:
Design Requirements:
- [ ] Accept input power from ~7.4V to 16V
- [ ] Convert to TBD internal power voltage
- [ ] When powered: Utilize internal power level to charge batteries, drive Servos, drive Control
- [ ] When unpowered: Utilize battery power to drive Servos, drive Control
- [ ] Transition from powered to unpowered should not cause power interruption for servos or control
- [ ] Self-Shutdown line from WROOM (kill power until supply reset)
- [ ] External connections must be vibration tolerant.
- [ ] Support tachometer signal at power voltage
- [ ] Servo operating range: 5V to 9V (ideally 6V to 7.4V)
- [ ] Function as motherboard for WROOM esp32, especially USB to UART function
- [ ] Should be able to power and flash WROOM esp32 via USB without powering the rest of the circuit (Except LEDs)
- [ ] Support LED control via DotStar protocol (SPI)
- [ ] Batteries are two LiPos, total voltage 7.4V nominal
- [ ] Onboard status LED
- [ ] Flash LEDs as warning when board is plugged in to USB

Flynnn, 2019-06-16:
Current requirements:
2 Servos: Hi-Tec HSB-9475-SH
For each servo: 900mA at 7.4V max.
Wroom: Less than 1100mA max at less than 4V.
DotStar one meter, 2000mA max at 5V.
Misc power budget: 1000mA max at 5V.

Total Power consumption: 32720 mAV (32.7 watts)
Total Power consumption, servos 4 A: 78600 mAV (78.6 watts)

Flynnn, 2019-06-16:
Appropriate power unit:
https://www.mouser.com/ProductDetail/ABB-Embedded-Power/APXW012A0X3-SRZ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

APXW012A0X3-SRZ

Flynnn, 2019-06-16:
Appropriate Battery Charge Circuit:
BQ2057WSNTR
https://www.mouser.com/ProductDetail/Texas-Instruments/BQ2057WSNTR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

Flynnn, 2019-06-16:
Connectors exceeding 3A should be JST-VH:
www.jst-mfg.com/product/pdf/eng/eVH.pdf

Flynnn, 2019-06-16:
JST-VH board mount vertical 3-pin:
https://www.digikey.com/product-detail/en/jst-sales-america-inc/B3P-VH-LF-SN/455-1640-ND/926548

Flynnn, 2019-06-16:
Main-Line Fuse:
https://www.digikey.com/product-detail/en/littelfuse-inc/0501010.WR/F1625CT-ND/2620103

Flynnn, 2019-06-17:
Aha!

AOD417
https://www.digikey.com/products/en?keywords=AOD417

Has a v_gs (th) between 1V and 3V, which means we can safely allow the supply voltage to be up to 0.9V less than the charge voltage. So if charge is 8.2, we can safely power the system on 7.3V

Flynnn, 2019-06-17:
In accordance with the above discovery, and moving forward with APXW012A0X3-SRDZ, I am speccing servo voltage at 7.5V. This will give us a minimum 0.1V safety margin if the charge voltage is set to 8.4V

Flynnn, 2019-06-18:
Recommend 9.95kohm trim resistor. Technically, this produces min junction voltage of 7.28V, which is slightly less than the absolute minimum of 7.3, but that minimum was designed to give 100mV margin from the *true* minimum which is 7.2. Speccing to 9.95kohm will yield 85mV margin in the absolute worst case.

Flynnn, 2019-06-18:
Charge rate will be 0.5A. Minimum battery voltage is 6V. Maximum input power is ~15V. Maximum Vdrop is 9V. Max power dissipation must be 150% 4.5W = 6.75W.

Charge controller CC current target recommended at 35mA. Beta must be at least  0.5A/35mA = 15. (IE, the only BJTs in existence that would fail this margin are the leftovers from when BJTs were first invented).

Flynnn, 2019-06-18:
STD2805

https://www.mouser.com/ProductDetail/STMicroelectronics/STD2805T4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

Seems appropriate

Flynnn, 2019-06-26:
For BQ2057T (or even BQ2057W) V_SNS is 125mv. Current sense resistor is calculated as 125mv/(0.5A) = 0.25 ohms.

Flynnn, 2019-06-26:
https://www.digikey.com/product-detail/en/stackpole-electronics-inc/CSR0603FKR250/CSR0603FKR250TR-ND/1742486 Looks like an appropriate sense resistor

Flynnn, 2019-06-26:
Run of the mill 1k resistors are good for the CC gate resistor and the TS voltage divider

Flynnn, 2019-06-26:
Power system is essentially done with the following exceptions:

Input power safety needs to be completed (TVS addition, and fuse re-spec).

Self-Shutdown needs to be implemented. Tie a series enhancement PMOS gate to raw input through large resistor, add low power SCR to ground? Once triggered, SCR will remain active and force the PMOS off. Need to spice it out to confirm.

Connector for servos needs to be added. Filter caps for servos need to be added.

Once these are done, all that will remain will be ESP3-related things.

petermccloud, 2019-07-22:
Identified brushes to be used to transfer vehicle power to the EVPR rotors.
https://www.helwigcarbon.com/shop/99-362361/
https://www.helwigcarbon.com/shop/11-313761/
Both are a copper graphite brush, grade K136 from Hellwig Carbon and have a very low voltage drop (<0.7 V). Capacity for 99-362361 is 11 amps, while the capacity for 11-313761 is 16 amps. Moving forward with the 11-313761 for now to ensure extra margin.

Flynnn, 2019-07-22:
I am second-guessing the inclusion of a TVS. I did find one here:
https://www.digikey.com/product-detail/en/littelfuse-inc/SP4023-01FTG-C/F6757CT-ND/5428761

But here is the problem:
These guys are basically a couple zeners which temporarily short the power supply and ground so that if input voltage goes past a certain threshold, the short causes a vdrop bringing the short back down.

The problem is that this shorting is high-current. If we put it after our fuse, it will basically cause the fuse to blow whenever there are transient voltage spikes, which we absolutely do not want to happen in flight.

We can't use the TVS without a fuse, as, were it to fail (rather than trip), it would create a permanent dead short.

Using the TVS with its own separate fuse is an option, but is getting on the edge of ridiculousness.

At the end of the day, I think having some faith in the output of the inverter, and using some good decoupling capacitors will be all that is necessary to prevent transient voltage spikes.

Flynnn, 2019-07-22:
1W, 2K resistors for latching power off:
https://www.digikey.com/product-detail/en/bourns-inc/CHV2512-FX-2204ELF/CHV2512-FX-2204ELFCT-ND/5176019

Flynnn, 2019-07-22:
Forget SCR! Can use a P-MOSFET flip flop instead.

I'm gonna use a third power FET for now, as I don't think the increase in cost or board space will be enough to cause any problems, and the re-use of components simplifies the design.

Flynnn, 2019-07-23:
Forget a third FET! While a flip-flop is possible, it will require 12V control logic. That can be achieved using a BJT, but then, why not just use the BJT directly? I will spec a BJT to be used for a latching shutdown.

Flynnn, 2019-07-23:
For the NPN controlling the shutdown latch:
https://www.digikey.com/product-detail/en/nexperia-usa-inc/PMBT4401235/1727-1886-1-ND/5015561
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
Flynnn, 2019-12-21:
P-channel equivalent to DMNl06k-7 https://www.digikey.com/product-detail/en/diodes-incorporated/BSS84-7-F/BSS84-FDICT-ND/717844

Flynnn, 2019-12-22:
ORING diode array for poweroff state power merge

https://www.digikey.com/product-detail/en/diodes-incorporated/SDM40E20LC-7/SDM40E20LC-7DICT-ND/2260642

Flynnn, 2019-12-27:
Power capacitor for DotStar
https://www.digikey.com/product-detail/en/nichicon/UWT0J102MNL1GS/493-2160-1-ND/590135

Flynnn, 2020-01-06:
Look at this chip later (alternative power merge FET):

petermccloud, 2020-01-08:
After our discussion with Andrew, I realized that a flow chart showing the various hardware operations would be helpful in my understanding of the schematic. I've created one under the master branch at:
https://github.com/mccloudaero/evpr/blob/master/operation_mode_diagram.md

I used mermaid, which isn't supported by Github Flavored Markdown, but may be someday. In the top of the markdown document there is a link to extensions for browsers to properly render the graph.

This will also give a good outline for developing the software at a later point.

petermccloud, 2020-01-08:
Our conversation regarding waking up the device got me thinking more about some of the ESP32 capabilities that might be useful. The ESP32 has some deep sleep modes and a ultra low power processor (in addition to the dual core main processor). The deep sleep mode can go as low as 1.5 microamps and can wake on a pin going high. https://lastminuteengineers.com/esp32-deep-sleep-wakeup-sources/

Perhaps instead of using a rising edge detector, use the RTC to wake on a pin going high (connected to VRAW). We can then can boot the ESP32 and enable the rest of the power? At 1.5 microamps  it'd take 100 years to drain the 1300mAh batteries. I'm not entirely sure how this would jive with the power merge/monitoring system though, so that would need to be figured out.

Flynnn, 2020-01-09:
Not a bad thought at all! The answer is that I would need to put the ESP32 on a special separate power bus that is just for it and can never be turned off. It would be a fairly significant change to the circuit, but I think this might actually be the correct solution, to be frank. It is pleasantly simple. I could kick myself for not coming up with it myself.

Flynnn, 2020-01-11:
17V TVS diode for brush sources:

https://www.digikey.com/product-detail/en/vishay-semiconductor-diodes-division/VESD16A2-03G-G3-08/VESD16A2-03G-G3-08GICT-ND/10229761

Flynnn, 2020-01-23:
- [0805 510 ohm CR0805-JW-511ELF](https://www.digikey.com/product-detail/en/bourns-inc/CR0805-JW-511ELF/CR0805-JW-511ELFCT-ND/4247984)

Flynnn, 2020-01-23:
Useful command: ATTRIBUTE X 'COMPONENT' 'xxx'; CHANGE DISPLAY OFF

Flynnn, 2020-01-23:
Right angle 2 pin (PINHD-1X2/90):
https://www.digikey.com/product-detail/en/w-rth-elektronik/61300211021/732-5335-ND/4846822

Flynnn, 2020-03-21:
New 3.3V regulator:
https://www.digikey.com/product-detail/en/diodes-incorporated/AP63203WU-7/AP63203WU-7DICT-ND/9858430

Flynnn, 2020-03-21:
Heads up, I am developing on a new branch, which I am referring to as REV2.

https://github.com/mccloudaero/evpr/tree/dev-mk2brd-rev2

Since we did a small prototyping run of the previous branch, I feel it is important to keep it in a vacuum for reference purposes for the time being.

Flynnn, 2020-03-22:
DESIGN NOTE:
Calculated currents from three sources:
From brushes: 4.5A @12V
~~From batteries: 7ishA @7.4V~~
From converter: 6.4A@8.4V

Flynnn, 2020-03-28:
Various connectors:
https://github.com/mccloudaero/evpr/issues/32

GeorgesOatesLarsen, 2020-07-30:
NOTE: Switching away from AOD transistors. For main power switching, utilizing
SI7997DP dual PFET. We do not use the second PFET, but the dual package is still smaller than AOD class packages.
https://www.digikey.com/product-detail/en/vishay-siliconix/SI7997DP-T1-GE3/SI7997DP-T1-GE3CT-ND/244207

It's rated for 60A which is ridiculously above our payload, but it looks like PFETs in this category basically have no chill -- anything lower than this capable of meeting VDSS requirements is sub 10 amps.

For power merging, instead of AOD, we are using CSD88537NDT which comes in an adorable 8-SOIC package and can handle 15A. Yeehaw.
https://www.digikey.com/product-detail/en/texas-instruments/CSD88537NDT/296-37795-2-ND/4862952

GeorgesOatesLarsen, 2020-07-31:
The MP2615 will be our new charge circuit. Will require new passives.
https://www.digikey.com/product-detail/en/monolithic-power-systems-inc/MP2615GQ-Z/1589-1610-1-ND/9433376

GeorgesOatesLarsen, 2020-11-23:
Helpful ESP32 Wroom spec sheet:
https://www.espressif.com/sites/default/files/documentation/esp32_datasheet_en.pdf

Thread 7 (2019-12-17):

Power Save Mode for battery sense does not work

Flynnn, 2019-12-17:
The current solution is nonsense, replace with better solution.

Flynnn, 2019-12-21:
Fixed. b334c16

High-Side control required to avoid defeating the purpose of the dividers by driving them high during power save mode.

So, should we use PFET or NFET for the high-side control? High-side control requires the introduction of a third FET in order to level shift up to the control voltage.

PFET is not practical as a level shifter (I'm sure you could figure it out, but it won't be simple), whereas NFET works great. The caveat is NFET must have source tied to ground.

We want high-side gates to default to OFF. If we pick NFET for them, their gates must be biased to ground. But this will make the level shifter useless since it shorts to ground. So, the high-side gates must be PFET.

In conclusion, power save uses two high-side PFETS driven by an NFET level shifter.

Closed 2019-12-21.

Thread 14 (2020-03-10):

Fab Process Improvements

Flynnn, 2020-03-10:
Purchase sufficient organizers
Create two organizers: One for top, one for bottom, parts that are both top and bottom are given a compartment in each.
We should buy metal stencils
Manufacture a board holder for stencils

Flynnn, 2020-03-22:
OK, so the board holder is pretty much off-limits as that will require EPL access which is impossible.

I stand by my advocation for metal stencils, though!

Flynnn, 2020-03-22:
Schematic is now complete, so I can generate a BOM and identify top/bottom part counts.

Flynnn, 2020-03-22:
There are about 47 unique part types. At maximum we will require 94 compartments, with 4 being large.

Recommend purchasing:
8 (x10) of: https://www.adafruit.com/product/431 ($31.6 total)
8 (x3)  of: https://www.adafruit.com/product/432 ($23.6 total)
8 (x2) of: https://www.adafruit.com/product/433 ($23.6 total)

This will result in 120 compartments. The extra overhead is to account for inaccuracies in my estimation on final part count and box size selections. It also allows for the addition of new parts later in the project if need be. The total for this purchase is $78.8 + shipping.

Flynnn, 2020-03-23:
Okay, with Adafruit out of business for the foreseeable future, let's just buy one of the 100pcs kits here:

https://www.amazon.com/20PCS-Electronic-Component-Laboratory-Storage/dp/B01NA9WOX1

It'll cost $32

I can't find anyone selling the small or medium sizes, but the tiny size should at least be useful for most of what we need to do.

petermccloud, 2020-03-23:
Power Supply for anodizing
https://www.caswellplating.com/electroplating-anodizing/power-supplies/cc-cv-rectifier-0-30v-30-amp.html

petermccloud, 2020-03-23:
DigiKey Boxes:
431- https://www.digikey.com/product-detail/en/adafruit-industries-llc/431/1528-1139-ND/5353599
432 - https://www.digikey.com/product-detail/en/adafruit-industries-llc/432/1528-1140-ND/5353600
433 - https://www.digikey.com/product-detail/en/adafruit-industries-llc/433/1528-1241-ND/5356726

Flynnn, 2020-03-23:
You're a legend; fire away on those DigikKey Boxes! @petermccloud

I still need to look at the PS

Flynnn, 2020-03-23:
That supply looks great! If that's what you want to order, by all means.

petermccloud, 2020-03-23:
@Flynnn I know you're looking for a quality hot air station. I did find the Quick 861DW [for $265 with free shipping](https://www.tequipment.net/Quick/861DW/Desoldering-Equipment/Rework-Stations/#description). However, looking at other options, I trust Adafruit and they also sell the Quick 957DW+, which I can [find for $95](https://www.tequipment.net/Quick/957DW+/Desoldering-Equipment/Rework-Stations/). Adding a 10 pack of different nozzle size brings it to $130. It's not AS stellar reviews, but still decent. Considering it's half the price, I'd need to be convinced to get the more expensive one.

petermccloud, 2020-03-23:
Ok. After looking over my anodizing requirements in more detail, a 10 amp supply should be more than sufficient. I'm looking at the next bigger size of what you pointed out, but the newer style supply which has a finer amperage control, which I'll need for anodizing.
https://www.amazon.com/dp/B07DQR177D/ref=emc_b_5_t

petermccloud, 2020-03-23:
@Flynnn Got everything ordered. Decided to just go with the more expensive hot air station. Ended up getting this power supply https://smile.amazon.com/dp/B073TW8H2S/ref=emc_b_5_t. It's just the 10A version of what you pointed me to. It has less noise and better voltage regulation than the newer style.

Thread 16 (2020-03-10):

Better silkscreen is needed

Flynnn, 2020-03-10:
Add our names, add component names too

Flynnn, 2020-03-21:
@petermccloud Would you be willing to copy a line-art Mccloud Aero logo for the silkscreen? Something that can be tiny, like fit in a 10mm by 7mm area?

petermccloud, 2020-03-21:
@Flynnn By line-art you mean SVG? Looks like I can't attach files here. I'll email you the files.

Flynnn, 2020-03-23:
```py
import pandas as pd
import re

pd.set_option('display.max_rows', None)
pd.set_option('display.max_columns', None)
pd.set_option('display.width', None)
pd.set_option('display.max_colwidth', -1)

bomraw = pd.read_csv('bomraw.csv', sep=';')
bom = bomraw[['Part', 'Value', 'COMPONENT']]

groups = {};

for part in bom['Part']:
    prefix = re.search(r'[a-zA-Z\.]+', part).group(0);
    if (prefix not in groups):
        groups[prefix] = []
    groups[prefix].append(part)

for k,v in groups.items():
    parts = v
    parts.sort(key = lambda part: int(re.search(r'[0-9]+', part).group(0)))
    n = 0
    for part in parts:
        n += 1
        prefix = re.search(r'[a-zA-Z\.]+', part).group(0)
        print(f'NAME {part} {prefix}{n};')
```

Flynnn, 2020-03-23:
NAME C.B13 C.B1;
NAME C.B32 C.B2;
NAME C.D15 C.D1;
NAME C.D21 C.D2;
NAME C.EJ1 C.EJ1;
NAME C.ES2 C.ES1;
NAME C.ES3 C.ES2;
NAME C.F9 C.F1;
NAME C.F12 C.F2;
NAME C.F15 C.F3;
NAME C.F17 C.F4;
NAME C.F20 C.F5;
NAME C.F26 C.F6;
NAME C.F35 C.F7;
NAME C.F36 C.F8;
NAME C.G39 C.G1;
NAME C.J27 C.J1;
NAME C.J28 C.J2;
NAME C.L30 C.L1;
NAME C.L31 C.L2;
NAME C.M1 C.M1;
NAME C.M2 C.M2;
NAME C.M3 C.M3;
NAME C.M4 C.M4;
NAME C.M5 C.M5;
NAME C.M10 C.M6;
NAME C.M29 C.M7;
NAME C.M40 C.M8;
NAME C.P16 C.P1;
NAME C.P22 C.P2;
NAME C.P23 C.P3;
NAME C.P24 C.P4;
NAME C.S37 C.S1;
NAME C.S38 C.S2;
NAME C.Y6 C.Y1;
NAME C.Y7 C.Y2;
NAME C.Y8 C.Y3;
NAME C.Y33 C.Y4;
NAME C.Z11 C.Z1;
NAME C.Z14 C.Z2;
NAME C.Z18 C.Z3;
NAME C.Z19 C.Z4;
NAME C.Z25 C.Z5;
NAME C.Z34 C.Z6;
NAME D.F3 D.F1;
NAME D.J1 D.J1;
NAME F.D1 F.D1;
NAME L.F20 L.F1;
NAME L.P2 L.P1;
NAME L.Z19 L.Z1;
NAME Q.B3 Q.B1;
NAME Q.F6 Q.F1;
NAME Q.F7 Q.F2;
NAME Q.J16 Q.J1;
NAME Q.K4 Q.K1;
NAME Q.L5 Q.L1;
NAME Q.L9 Q.L2;
NAME Q.L11 Q.L3;
NAME Q.Y1 Q.Y1;
NAME Q.Y2 Q.Y2;
NAME Q.Z8 Q.Z1;
NAME Q.Z10 Q.Z2;
NAME Q.Z13 Q.Z3;
NAME R.B3 R.B1;
NAME R.B4 R.B2;
NAME R.B5 R.B3;
NAME R.B6 R.B4;
NAME R.CD4 R.CD1;
NAME R.CD5 R.CD2;
NAME R.ED3 R.ED1;
NAME R.ED4 R.ED2;
NAME R.ES1 R.ES1;
NAME R.ES2 R.ES2;
NAME R.F17 R.F1;
NAME R.F18 R.F2;
NAME R.F19 R.F3;
NAME R.F30 R.F4;
NAME R.G10 R.G1;
NAME R.J15 R.J1;
NAME R.J20 R.J2;
NAME R.J21 R.J3;
NAME R.J22 R.J4;
NAME R.J23 R.J5;
NAME R.K9 R.K1;
NAME R.K28 R.K2;
NAME R.L24 R.L1;
NAME R.L25 R.L2;
NAME R.L26 R.L3;
NAME R.L27 R.L4;
NAME R.L33 R.L5;
NAME R.L34 R.L6;
NAME R.M1 R.M1;
NAME R.M8 R.M2;
NAME R.M11 R.M3;
NAME R.M32 R.M4;
NAME R.P12 R.P1;
NAME R.P13 R.P2;
NAME R.P14 R.P3;
NAME R.P16 R.P4;
NAME R.Y7 R.Y1;
NAME SJ.K2 SJ.K1;
NAME T.P3 T.P1;
NAME T.P5 T.P2;
NAME TP.B6 TP.B1;
NAME TP.F9 TP.F1;
NAME TP.F10 TP.F2;
NAME TP.F11 TP.F3;
NAME TP.F18 TP.F4;
NAME TP.J2 TP.J1;
NAME TP.J3 TP.J2;
NAME TP.L4 TP.L1;
NAME TP.L8 TP.L2;
NAME TP.M5 TP.M1;
NAME TP.M7 TP.M2;
NAME TP.P13 TP.P1;
NAME TP.P14 TP.P2;
NAME TP.P15 TP.P3;
NAME TP.P16 TP.P4;
NAME TP.P19 TP.P5;
NAME TP.Y1 TP.Y1;
NAME TP.Z12 TP.Z1;
NAME TP.Z17 TP.Z2;
NAME U.B1 U.B1;
NAME U.D6 U.D1;
NAME U.F2 U.F1;
NAME U.G3 U.G1;
NAME U.P12 U.P1;
NAME U.Y8 U.Y1;
NAME U.Z17 U.Z1;
NAME U7 U1;
NAME X.D5 X.D1;
NAME X.F1 X.F1;
NAME X.G1 X.G1;
NAME X.J1 X.J1;
NAME X.K1 X.K1;
NAME X.L1 X.L1;
NAME X.L2 X.L2;
NAME X.S2 X.S1;
NAME X.S3 X.S2;
NAME X.S4 X.S3;

Flynnn, 2020-03-23:
All components now follow new naming scheme: 76222ff

Scheme is as follows:

A.BXXX

where A is the component type prefix (U, Q, L, D, R, C, X, TP, SJ), and B is the block prefix (describing the functional block of origin for the part), and XXX is a unique number within the particular block/type prefix, counting starting from 1

Flynnn, 2020-03-25:
[mccloud_aero_logo_tiny_fo_silkscreen_202003.dxf.zip](https://github.com/mccloudaero/evpr/files/4384275/mccloud_aero_logo_tiny_fo_silkscreen_202003.dxf.zip)

Flynnn, 2020-03-25:
[mccloud_aero_logo_tiny_fo_silkscreen_20200_mm.dxf.zip](https://github.com/mccloudaero/evpr/files/4384295/mccloud_aero_logo_tiny_fo_silkscreen_20200_mm.dxf.zip)

Flynnn, 2020-03-25:
[mccloud_aero_logo_tiny_fo_silkscreen_202003.svg.zip](https://github.com/mccloudaero/evpr/files/4384311/mccloud_aero_logo_tiny_fo_silkscreen_202003.svg.zip)

Flynnn, 2020-03-26:
[Market_Deco.ttf.zip](https://github.com/mccloudaero/evpr/files/4384323/Market_Deco.ttf.zip)

Flynnn, 2020-03-26:
Complete  f3e1695

Closed 2020-03-26.

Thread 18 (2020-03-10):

Change connectors for DotStar, and for PAD (Passive Absorption Device)

Flynnn, 2020-03-10:
PAD needs a locking connector, and DotStar is just obnoxiously huge.

Flynnn, 2020-03-22:
Recommend JST PA for DotStar; Locking connector, supports board mount, 2.0 mm pitch.

Flynnn, 2020-03-22:
JST PA 4POS: BM04B-PASS-1-TFT(LF)(SN)
https://www.digikey.com/product-detail/en/jst-sales-america-inc/BM04B-PASS-1-TFT-LF-SN/455-2639-1-ND/2773434

Flynnn, 2020-03-22:
JST PA also has sufficient current rating for our servos. (roughly twice what is required, in fact). So, for space savings, recommend switching servo connectors to JST PA

By extension, this will work for the PAD as well! So only our batteries need to be the big brother, JST VH

Just double checked power calculations. Yes, our upstream power sources (Batteries / brushes) need to withstand closer 4.5A and 7.25A respectively. The converter will need to produce 6.4A.

Flynnn, 2020-03-22:
Completed. 087ae47

Closed 2020-03-22.

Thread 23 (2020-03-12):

Deep sleep architecture must be changed

Flynnn, 2020-03-12:
Suggestion: Drive the non-battery enable pin on the power merger. Also add and drive an enable/disable transistor on the USB to serial interface.

Flynnn, 2020-03-21:
OK!

Been going on a bit of a deep dive. Let's examine what power save looks like.

When we are running solely on battery, we have the following power sinks:

1. Battery Sense Dividers
1. Power Merge System
1. 5V Converter
1. 3.3V Converter
1. Serial Interface
1. ESP32
1. DotStar Interface
1. DotStars
1. Servos

I'm told that the serial interface is an absolute power hog when idle. Fortunately, it comes with a builtin linear regulator and can be configured to rely directly on USB power. This means we don't even have to consider its quiescent power consumption.

The Battery Sense Dividers are also nearly eliminated from consideration thanks to the power save transistors we installed earlier. They will default to not operating when the ESP32 goes into deep sleep. Transistors of this kind ***do*** have quiescent current, though, and for the battery sense system this will amount to less than 3 uA total (and will likely be closer to 330nA)

The ESP32, in deep sleep, draws 100uA. Our 5V regulator is a switching  regulator that is about 70% efficient in its ultralow current domain, so the worst case conversion factor for battery-level current will be 5V/7.2v * 1/0.7  = 0.992. Hilarious. Might as well be a linear regulator in the low current domain. So we'll call it 100uA at the battery.

The converter itself has a quiescent current of 22uA.

Our 3.3v converter has a quiescent current of 55uA.

The power merge system has pretty intense quiescent current draw of about 3mA (wow). If we can somehow disable both channels (more on that later), that value gets reduced to 160uA.

I can't remember how many DotStars we are dealing with, but each pixel costs 1mA in quiescent, so assuming 32 pixels, we are talking about 32mA of quiescent current. A means by which to totally starve the DotStars of their power when inactive is absolutely critical.

Similar situation for the servos, each one draws 7mA when idle. We need a way to specifically starve them of power.

The DotStar Interface basically costs 82uA. Pretty small all things considered.

We have essentially three options:

Firstly, we can keep everything as it is, with the ESP32's supplies downstream of the power merger, and no on-off transistors for everything. Our "deep sleep" current would then be 3uA + 100uA + 22uA + 55uA + 32mA + 3mA + 14mA + 82uA = 49.26mA, corresponding to about 13 hours of idle battery life.

Secondly, we can be a bit more strategic, keep a minimal-converter design with the ESP32 downstream of the merger, but add an a couple large power transistors for the peripherals. This would get us down to 3uA + 100uA + 22uA + 55uA + 3mA + 82uA = 3.262 mA, or about 199 hours of idle battery life (8 or so days). However, this carries the very serious downside of effectively doubling the number of power transistors we have. These power transistors are one of the largest components on the board, and would cost quite a bit of space, and would have the ***additional*** downside of worsening power efficiency. All-in-all I can't recommend this approach.

The third and final approach is to use "redundant" (more on that later) power supplies. This feels icky, but it has the highest simplicity, power efficiency, and board space efficiency of all three options (technically all four if you consider the ***original*** solution before rev 2). Give the ESP32 its own 3.3V regulator fed by a diode power merge circuit totally independent of the main power system. In fact, if we do that, we will no longer even need the original 3.3V regulator since I switched the serial interface over to its internal supply. Wow. This isn't even redundant. Okay, not icky at all. To reiterate:

Take the 3.3V regulator feeding the ESP32 off of the 5.0V rail, since nothing else uses it anymore, and feed it directly from a simple diode power merger between the main converter / batteries. This will have lower power efficiency since it is converting from around 8V rather than 5V, but it will enable the ESP32 to control the enable/disable pin on the main power merger, which we can use as a method to starve the rest of the system of power when in shutdown mode.

Under this system, when in power save mode, only the following would even be receiving power:

1. Battery Sense Dividers
1. Power Merge System
1. 3.3V Converter
1. ESP32

And the power merge system could be fully disabled, leading to a total current consumption of 3uA + 55uA + 160uA + 100uA = 2044 hours (85 days).

This is, IMO, the best decision. Moving forward with it. Still need to double check the 3.3V regulator can handle 8V, but I don't expect it can't.

Flynnn, 2020-03-21:
Slight correction: We should do a ***three*** way diode power merger between BAT, VCONV, and VUSB so that the esp32 can also be powered from the USB port.

Flynnn, 2020-03-21:
Unfortunately, the 3.3V converter we have selected supports only up to 6V. This being stated, our 5.0V regulator mentions a 3.3V version we could use which has the added benefit of being a switching regulator meaning the power efficiency drawbacks would be moot, at the expense of needing a decent number of extra SMD components. Will investigate. Still more space efficient than any other solutions thus far.

Flynnn, 2020-03-21:
Yeah, the AP63203WU-7 will absolutely do the trick. Frankly it is like 4x overkill on current supply. But I'll take the devil I know over the devil I have to select new passives for : - )

Flynnn, 2020-03-21:
I found a much lower profile rectifier diode (SMD34LHE1-TP). The lower profile comes at the cost of a higher forward voltage, which won't matter since we are either regulating down to 3.3V, or directly supplying DotStars.

Flynnn, 2020-03-21:
Whooaa. Just noticed the inductors we have selected have a saturation current that is way too low. Saturation current needs to be 1.3A on all of them.

Flynnn, 2020-03-21:
Looks like
SRR4818A-4R7Y  for the 4.7uH (1.5A sat / 80 mOhm) (https://www.digikey.com/product-detail/en/bourns-inc/SRR4818A-4R7Y/SRR4818A-4R7YCT-ND/7556055)

SRR4818A-3R9Y for the 3.9uH (1.9A sat / 80mOhm) (https://www.digikey.com/product-detail/en/bourns-inc/SRR4818A-3R9Y/SRR4818A-3R9YCT-ND/7556054)

Flynnn, 2020-03-21:
Closed 381eb20

Flynnn, 2020-03-21:
Closed 381eb20

Closed 2020-03-21.

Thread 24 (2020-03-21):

EVPR MK2 Rev 2 Parts Selection

Flynnn, 2020-03-21:
This issue is a part selection notebook for the second revision of the MK2 EVPR board.

Flynnn, 2020-03-21:
4.7uF 20% 0603 capacitor: CL10A475MQ8NNNC
https://www.digikey.com/product-detail/en/samsung-electro-mechanics/CL10A475MQ8NNNC/1276-1907-1-ND/3889993

Flynnn, 2020-03-21:
0.1uF 5% 0603 capacitor: 06033C104JAT2A
https://www.digikey.com/product-detail/en/avx-corporation/06033C104JAT2A/478-3713-1-ND/1116411

Flynnn, 2020-03-21:
450mV/3A SOD-123H Rectifier Diode: SMD34LHE1-TP
https://www.mccsemi.com/pdf/Products/SMD34LHE1(SOD-123HE1)-A.pdf

Flynnn, 2020-03-21:
4.7uH (1.5A sat / 80 mOhm): SRR4818A-4R7Y
https://www.digikey.com/product-detail/en/bourns-inc/SRR4818A-4R7Y/SRR4818A-4R7YCT-ND/7556055

Flynnn, 2020-03-21:
3.9uH (1.9A sat / 80mOhm): SRR4818A-3R9Y
https://www.digikey.com/product-detail/en/bourns-inc/SRR4818A-3R9Y/SRR4818A-3R9YCT-ND/7556054

Flynnn, 2020-03-22:
56µF 6.3mm Electrolytic: APXG250ARA560MF61G  [OLD since last rev]
https://www.digikey.com/product-detail/en/united-chemi-con/APXG250ARA560MF61G/565-4303-1-ND/5824824

Flynnn, 2020-03-22:
37.4 kOhm 1% 0603: RC0603FR-0737K4L
https://www.digikey.com/product-detail/en/yageo/RC0603FR-0737K4L/311-37-4KHRCT-ND/730134

Flynnn, 2020-03-22:
768ohm 0603: RMCF0603FT768R
https://www.digikey.com/product-detail/en/stackpole-electronics-inc/RMCF0603FT768R/RMCF0603FT768RCT-ND/6053173

Flynnn, 2020-03-22:
JST PA 4POS: BM04B-PASS-1-TFT(LF)(SN)
https://www.digikey.com/product-detail/en/jst-sales-america-inc/BM04B-PASS-1-TFT-LF-SN/455-2639-1-ND/2773434

Flynnn, 2020-03-22:
JST PA also has sufficient current rating for our servos. (roughly twice what is required, in fact). So, for space savings, recommend switching servo connectors to JST PA

Flynnn, 2020-03-22:
By extension, this will work for the PAD as well! So only our batteries need to be the big brother, JST VH

Flynnn, 2020-03-22:
JST PA 3POS: BM03B-PASS-1-TFT(LF)(SN)
https://www.digikey.com/product-detail/en/jst-sales-america-inc/BM03B-PASS-1-TFT-LF-SN/455-2638-1-ND/2773433

JST PA 2POS: BM02B-PASS-1-TFT(LF)(SN)
https://www.digikey.com/product-detail/en/jst-sales-america-inc/BM03B-PASS-1-TFT-LF-SN/455-2638-1-ND/2773433

Flynnn, 2020-03-22:
Just double checked power calculations. Yes, our upstream power sources (Batteries / brushes) need to withstand closer 4.5A and 7.25A respectively. The converter will need to produce 6.4A.

Flynnn, 2020-03-22:
22uF 0603 GRM188R61A106KE69D:
https://www.digikey.com/product-detail/en/murata-electronics/GRM188R61A106KE69D/490-10474-1-ND/5026392

Flynnn, 2020-03-22:
22uF 0603: CL10A226MO7JZNC
https://www.digikey.com/product-detail/en/samsung-electro-mechanics/CL10A226MO7JZNC/1276-7076-1-ND/7320718

Flynnn, 2020-03-22:
1kohm 0603 RMCF0603FT1K00:
https://www.digikey.com/product-detail/en/stackpole-electronics-inc/RMCF0603FT1K00/RMCF0603FT1K00CT-ND/1942996

Flynnn, 2020-03-22:
1Mohm 0603: RMCF0603FG1M00
https://www.digikey.com/product-detail/en/stackpole-electronics-inc/RMCF0603FG1M00/RMCF0603FG1M00CT-ND/4425038

Flynnn, 2020-03-22:
1Mohm 0603: RMCF0603FT100K
https://www.digikey.com/product-detail/en/stackpole-electronics-inc/RMCF0603FT100K/RMCF0603FT100KCT-ND/1943118

Flynnn, 2020-03-22:
22.1kohm RMCF0603FT22K1:
https://www.digikey.com/product-detail/en/stackpole-electronics-inc/RMCF0603FT22K1/RMCF0603FT22K1CT-ND/1943077

Flynnn, 2020-03-22:
95.3k 0603: RMCF0603FT95K3
https://www.digikey.com/product-detail/en/stackpole-electronics-inc/RMCF0603FT95K3/RMCF0603FT95K3CT-ND/2418160

Flynnn, 2020-03-22:
10kohm 0.1% RG1608P-103-B-T5:
https://www.digikey.com/product-detail/en/susumu/RG1608P-103-B-T5/RG16P10-0KBCT-ND/1240835

Flynnn, 2020-03-22:
47.5kohm 0603: RMCF0603FT47K5
https://www.digikey.com/product-detail/en/stackpole-electronics-inc/RMCF0603FT47K5/RMCF0603FT47K5CT-ND/1943100

Flynnn, 2020-03-22:
300ohm 0603: RMCF0603JT300R
https://www.digikey.com/product-detail/en/stackpole-electronics-inc/RMCF0603JT300R/RMCF0603JT300RCT-ND/2418198

Flynnn, 2020-03-22:
10kohm 0603: RMCF0603FT10K0
https://www.digikey.com/product-detail/en/stackpole-electronics-inc/RMCF0603FT10K0/RMCF0603FT10K0CT-ND/1943057

GeorgesOatesLarsen, 2020-07-31:
33uH 5040 1.3A 180mOhm: SRN5040TA-330M\
https://www.digikey.com/product-detail/en/bourns-inc/SRN5040TA-330M/SRN5040TA-330MCT-ND/9653909

GeorgesOatesLarsen, 2020-07-31:
0.47uF 0603 ceramic: C0603C474K4PACTU
https://www.digikey.com/product-detail/en/kemet/C0603C474K4PACTU/399-7934-1-ND/3471657

GeorgesOatesLarsen, 2020-07-31:
1uF 0603 ceramic: CL10A105KP8NNNC
https://www.digikey.com/product-detail/en/samsung-electro-mechanics/CL10A105KP8NNNC/1276-1182-1-ND/3889268

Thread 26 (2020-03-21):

EMI Odds & Ends

Flynnn, 2020-03-21:
Add bypass capacitors to all power sinks and entries

Flynnn, 2020-03-22:
Ensure all digital signals leaving or entering board have optional 0603 EMI slots.

EMI optionals will be prefixed with "E" for "EMI"

Flynnn, 2020-03-22:
Useful:
https://emcfastpass.com/avoid-the-most-common-failures-with-these-7-essential-emc-design-rules/

Flynnn, 2020-03-22:
Completed. 5fa7c3c

Closed 2020-03-22.

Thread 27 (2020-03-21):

Resize as many componets as possible to 0603

Flynnn, 2020-03-21:

Flynnn, 2020-03-22:
Components being targeted:

1. R15
1. R20
1. R21
1. R22
1. R23
1. R32
1. R1
1. R5
1. R6
1. R4
1. R34
1. R33
1. R24
1. R25
1. R26
1. R27
1. R7
1. [return to Deep Sleep Power]

Values required:
1. 500ohm
1. 100k
1. 22.1k
1. 95.3k (perfect match for R32)
1. (10k 0.1%)
1. 1k
1. 47.5k
1. 10k

Flynnn, 2020-03-22:
REPLACE X R-US_R0603
ATTRIBUTE X 'COMPONENT' 'xxx'; CHANGE DISPLAY OFF

Flynnn, 2020-03-22:
```python
import pandas as pd

pd.set_option('display.max_rows', None)
pd.set_option('display.max_columns', None)
pd.set_option('display.width', None)
pd.set_option('display.max_colwidth', -1)

bomraw = pd.read_csv('bomraw.csv', sep=';')
targets = ['R15','R20','R21','R22','R23','R32','R1','R5','R6','R4','R34','R33','R24','R25','R26','R27','R7','R30','R18','R19','R17','R12','R16','R13','R14','R9','R28','R10','C17','C14','C11','C19','C15','C20']
bom = bomraw[['Part', 'Value', 'COMPONENT']][bomraw['Part'].isin(targets)]
print(bom)
print(f'{len(bom)} == {len(targets)}? {len(bom) == len(targets)}')

valmap = {
'22uF':'CL10A226MO7JZNC',
'10uF':'GRM188R61A106KE69D',
'10k':'RMCF0603FT10K0',
'10k 0.1%':'RG1608P-103-B-T5',
'100k':'RMCF0603FT100K',
'1k':'RMCF0603FT1K00',
'300Ω':'RMCF0603JT300R',
'95.3kΩ':'RMCF0603FT95K3',
'22.1k':'RMCF0603FT22K1',
'47.5k':'RMCF0603FT47K5',
'1M':'RMCF0603FG1M00',
'47.5K':'RMCF0603FT47K5'
}

for index, row in bom.iterrows():
    device = 'R-US_R0603'
    if (row['Part'][0] == 'C'):
        device = 'C-USC0603'
    print(f'REPLACE {row["Part"]} {device}')
    print(f'ATTRIBUTE {row["Part"]} \'COMPONENT\' \'{valmap[row["Value"]]}\'; CHANGE DISPLAY OFF')```

Flynnn, 2020-03-22:
REPLACE C11 C-USC0603
ATTRIBUTE C11 'COMPONENT' 'CL10A226MO7JZNC'; CHANGE DISPLAY OFF
REPLACE C14 C-USC0603
ATTRIBUTE C14 'COMPONENT' 'GRM188R61A106KE69D'; CHANGE DISPLAY OFF
REPLACE C15 C-USC0603
ATTRIBUTE C15 'COMPONENT' 'CL10A226MO7JZNC'; CHANGE DISPLAY OFF
REPLACE C17 C-USC0603
ATTRIBUTE C17 'COMPONENT' 'GRM188R61A106KE69D'; CHANGE DISPLAY OFF
REPLACE C19 C-USC0603
ATTRIBUTE C19 'COMPONENT' 'CL10A226MO7JZNC'; CHANGE DISPLAY OFF
REPLACE C20 C-USC0603
ATTRIBUTE C20 'COMPONENT' 'CL10A226MO7JZNC'; CHANGE DISPLAY OFF
REPLACE R1 R-US_R0603
ATTRIBUTE R1 'COMPONENT' 'RG1608P-103-B-T5'; CHANGE DISPLAY OFF
REPLACE R4 R-US_R0603
ATTRIBUTE R4 'COMPONENT' 'RMCF0603FT1K00'; CHANGE DISPLAY OFF
REPLACE R5 R-US_R0603
ATTRIBUTE R5 'COMPONENT' 'RMCF0603FT100K'; CHANGE DISPLAY OFF
REPLACE R6 R-US_R0603
ATTRIBUTE R6 'COMPONENT' 'RMCF0603FT100K'; CHANGE DISPLAY OFF
REPLACE R7 R-US_R0603
ATTRIBUTE R7 'COMPONENT' 'RMCF0603FT10K0'; CHANGE DISPLAY OFF
REPLACE R9 R-US_R0603
ATTRIBUTE R9 'COMPONENT' 'RMCF0603FT10K0'; CHANGE DISPLAY OFF
REPLACE R10 R-US_R0603
ATTRIBUTE R10 'COMPONENT' 'RMCF0603FT10K0'; CHANGE DISPLAY OFF
REPLACE R12 R-US_R0603
ATTRIBUTE R12 'COMPONENT' 'RMCF0603FT1K00'; CHANGE DISPLAY OFF
REPLACE R13 R-US_R0603
ATTRIBUTE R13 'COMPONENT' 'RMCF0603FT10K0'; CHANGE DISPLAY OFF
REPLACE R14 R-US_R0603
ATTRIBUTE R14 'COMPONENT' 'RMCF0603FT10K0'; CHANGE DISPLAY OFF
REPLACE R15 R-US_R0603
ATTRIBUTE R15 'COMPONENT' 'RMCF0603FT1K00'; CHANGE DISPLAY OFF
REPLACE R16 R-US_R0603
ATTRIBUTE R16 'COMPONENT' 'RMCF0603JT300R'; CHANGE DISPLAY OFF
REPLACE R17 R-US_R0603
ATTRIBUTE R17 'COMPONENT' 'RMCF0603JT300R'; CHANGE DISPLAY OFF
REPLACE R18 R-US_R0603
ATTRIBUTE R18 'COMPONENT' 'RMCF0603FT22K1'; CHANGE DISPLAY OFF
REPLACE R19 R-US_R0603
ATTRIBUTE R19 'COMPONENT' 'RMCF0603FT47K5'; CHANGE DISPLAY OFF
REPLACE R20 R-US_R0603
ATTRIBUTE R20 'COMPONENT' 'RMCF0603FT100K'; CHANGE DISPLAY OFF
REPLACE R21 R-US_R0603
ATTRIBUTE R21 'COMPONENT' 'RMCF0603FT22K1'; CHANGE DISPLAY OFF
REPLACE R22 R-US_R0603
ATTRIBUTE R22 'COMPONENT' 'RMCF0603FT100K'; CHANGE DISPLAY OFF
REPLACE R23 R-US_R0603
ATTRIBUTE R23 'COMPONENT' 'RMCF0603FT22K1'; CHANGE DISPLAY OFF
REPLACE R24 R-US_R0603
ATTRIBUTE R24 'COMPONENT' 'RMCF0603FT47K5'; CHANGE DISPLAY OFF
REPLACE R25 R-US_R0603
ATTRIBUTE R25 'COMPONENT' 'RMCF0603FT22K1'; CHANGE DISPLAY OFF
REPLACE R26 R-US_R0603
ATTRIBUTE R26 'COMPONENT' 'RMCF0603FT47K5'; CHANGE DISPLAY OFF
REPLACE R27 R-US_R0603
ATTRIBUTE R27 'COMPONENT' 'RMCF0603FT22K1'; CHANGE DISPLAY OFF
REPLACE R28 R-US_R0603
ATTRIBUTE R28 'COMPONENT' 'RMCF0603FT10K0'; CHANGE DISPLAY OFF
REPLACE R30 R-US_R0603
ATTRIBUTE R30 'COMPONENT' 'RMCF0603FG1M00'; CHANGE DISPLAY OFF
REPLACE R32 R-US_R0603
ATTRIBUTE R32 'COMPONENT' 'RMCF0603FT95K3'; CHANGE DISPLAY OFF
REPLACE R33 R-US_R0603
ATTRIBUTE R33 'COMPONENT' 'RMCF0603FT100K'; CHANGE DISPLAY OFF
REPLACE R34 R-US_R0603
ATTRIBUTE R34 'COMPONENT' 'RMCF0603FT100K'; CHANGE DISPLAY OFF

Flynnn, 2020-03-22:
Completed. dd21e89

Closed 2020-03-22.

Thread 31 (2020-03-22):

Fix USB Footprint

Flynnn, 2020-03-22:
Currently creates board level short. Fix.

Flynnn, 2020-03-24:
Completed. 001809e

Closed 2020-03-24.

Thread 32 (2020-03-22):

Source cable connectors for all board connectors.

Flynnn, 2020-03-22:

Flynnn, 2020-03-28:
Contacts for JST-VH:
SVH-21T-P1.1: https://www.digikey.com/product-detail/en/jst-sales-america-inc/SVH-21T-P1-1/455-1133-1-ND/527367
SVH-41T-P1.1: https://www.digikey.com/product-detail/en/jst-sales-america-inc/SVH-41T-P1-1/455-1319-1-ND/608888

Housings for JST-VH:
VHR-2M: https://www.digikey.com/products/en?keywords=VHR-2M
VHR-3M: https://www.digikey.com/products/en?keywords=VHR-3M

Contacts for JST-PA:
SPHD-001T-P0.5: https://www.digikey.com/product-detail/en/jst-sales-america-inc/SPHD-001T-P0-5/455-1325-1-ND/608808

Housings for JST-PA:
PAP-02V-S: https://www.digikey.com/products/en?keywords=PAP-02V-S
PAP-03V-S: https://www.digikey.com/products/en?keywords=PAP-03V-S
PAP-04V-S: https://www.digikey.com/products/en?keywords=PAP-04V-S

Closed 2020-03-28.

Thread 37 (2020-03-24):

Replace 0603 capacitors with in-house component

Flynnn, 2020-03-24:
The default footprint has ridiculous tkeepout. Need to adjust to better fit our fab capabilities

Flynnn, 2020-03-24:
```py
import pandas as pd

pd.set_option('display.max_rows', None)
pd.set_option('display.max_columns', None)
pd.set_option('display.width', None)
pd.set_option('display.max_colwidth', -1)

bomraw = pd.read_csv('bomraw', sep=';')
bom = bomraw[['Part', 'Device']][bomraw['Device'].isin(['CC0603','R-US_R0603'])]

dmap = {
    'CC0603':'C0603',
    'R-US_R0603':'R0603'
}

for index, row in bom.iterrows():
    ndev = dmap[row['Device']]
    print(f'REPLACE {row["Part"]} {ndev};')
```

Flynnn, 2020-03-24:
REPLACE C.B1 C0603;
REPLACE C.B2 C0603;
REPLACE C.D2 C0603;
REPLACE C.EJ1 C0603;
REPLACE C.ES1 C0603;
REPLACE C.ES2 C0603;
REPLACE C.F1 C0603;
REPLACE C.F2 C0603;
REPLACE C.F6 C0603;
REPLACE C.F7 C0603;
REPLACE C.F8 C0603;
REPLACE C.G1 C0603;
REPLACE C.J1 C0603;
REPLACE C.J2 C0603;
REPLACE C.L1 C0603;
REPLACE C.L2 C0603;
REPLACE C.M7 C0603;
REPLACE C.M8 C0603;
REPLACE C.P1 C0603;
REPLACE C.P2 C0603;
REPLACE C.P3 C0603;
REPLACE C.P4 C0603;
REPLACE C.S1 C0603;
REPLACE C.S2 C0603;
REPLACE C.Y1 C0603;
REPLACE C.Y2 C0603;
REPLACE C.Y3 C0603;
REPLACE C.Y4 C0603;
REPLACE C.Z3 C0603;
REPLACE C.Z5 C0603;
REPLACE C.Z6 C0603;
REPLACE R.B1 R0603;
REPLACE R.B2 R0603;
REPLACE R.B3 R0603;
REPLACE R.B4 R0603;
REPLACE R.CD1 C0603;
REPLACE R.CD2 C0603;
REPLACE R.ED1 R0603;
REPLACE R.ED2 R0603;
REPLACE R.ES1 R0603;
REPLACE R.ES2 R0603;
REPLACE R.F1 R0603;
REPLACE R.F2 R0603;
REPLACE R.F3 R0603;
REPLACE R.F4 R0603;
REPLACE R.G1 R0603;
REPLACE R.J1 R0603;
REPLACE R.J2 R0603;
REPLACE R.J3 R0603;
REPLACE R.J4 R0603;
REPLACE R.J5 R0603;
REPLACE R.K1 R0603;
REPLACE R.K2 R0603;
REPLACE R.L1 R0603;
REPLACE R.L2 R0603;
REPLACE R.L3 R0603;
REPLACE R.L4 R0603;
REPLACE R.L5 R0603;
REPLACE R.L6 R0603;
REPLACE R.M1 R0603;
REPLACE R.M2 R0603;
REPLACE R.M3 R0603;
REPLACE R.M4 R0603;
REPLACE R.P1 R0603;
REPLACE R.P2 R0603;
REPLACE R.P3 R0603;
REPLACE R.P4 R0603;
REPLACE R.Y1 R0603;

Closed 2020-03-24.

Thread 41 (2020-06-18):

Adjust C.M1 and C.M2 packages

GeorgesOatesLarsen, 2020-06-18:
Currently have to be hand-soldered due to slight package mismatch

GeorgesOatesLarsen, 2020-10-11:
Now Corrected

Closed 2020-10-11.

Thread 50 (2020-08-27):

Stencil Variant Testing

GeorgesOatesLarsen, 2020-08-27:
Need to test some stencil variants

GeorgesOatesLarsen, 2020-08-27:
[stenciltesting2.zip](https://github.com/mccloudaero/evpr/files/5138704/stenciltesting2.zip)

GeorgesOatesLarsen, 2020-09-22:
Variants:

Variant A:
Power mini pads are 0.2mm x 1.1mm
Power corner pads are 1.05mm x 1.55mm
Power mainline pads are 1.15mm x 1.55mm
Charger Pads are 0.2mm wide.

Variant B:
Charger pads are 0.150mm wide
Power mini pads are 0.2mm x 1.1mm
Power corner pads are 0.9mm x 1.4mm
Power mainline pads are 1mm x 1.4mm

Variant C:
Charger pads are 0.100mm wide
Power mini pads are 0.2mm x 1.1mm
Power corner pads are 0.9mm x 1.4mm
Power mainline pads are 0.85mm x 1.4mm

GeorgesOatesLarsen, 2020-09-22:
Variant C is 100% the way to go for the power module. Cleanest I have ever seen it. Circuit operates as intended (finally. ugh.)

GeorgesOatesLarsen, 2020-09-22:
Stress testing confirms nominal behavior up to 4A output

GeorgesOatesLarsen, 2020-09-23:
Variant B is ideal for charger module. Gives clean results. Battery charge module behaves nominally and successfully charged two cells to 8.34V as measured

Closed 2020-09-23.

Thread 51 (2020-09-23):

Possibly adjust target voltages

GeorgesOatesLarsen, 2020-09-23:
Charging terminal voltage is somewhat close to nominal output voltage of converter. Suggest raising converter target voltage by 0.1V (this amounts to swapping out a couple of resistors), or, alternatively, altering the charge mode of the charger IC.

Verify that voltages are actually too close to one-another for comfort before making these changes.

GeorgesOatesLarsen, 2021-09-30:
This is a non-issue, closing

Closed 2021-09-30.

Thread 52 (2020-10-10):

Rename All Components

GeorgesOatesLarsen, 2020-10-10:
Component identifiers are out-of-date. They need to be reworked. Perform mass renaming. (Need to dig up the scripts I wrote to help with this...)

GeorgesOatesLarsen, 2020-10-11:
#12 is the relevant issue

GeorgesOatesLarsen, 2020-10-11:
I am altering the naming convention.

In particular, the EMC optional components will be named differently.

Non-EMC components will be named as follows:

`XX.YY\#\#`

EMC components will be named as follows:

`XX.YY\*\#\#`

Here, XX is the part type, one of:

- C: Capacitor
- D: LED
- L: Inductor
- Q: Transistor
- R: Resistor
- S: Solder Jumper
- TP: Test Point
- U: Integrated Circuit
- X: Connector

Y is the functional group code, one of:
- BC: Battery Charge control
- EC: Engine power Conversion
- EI: Engine power & tachometer Interface
- BI: Battery Interface
- MY: SYS_POWER Management
- ZZ: Sleep Management & Power
- USB: USB Interface
- ESP: ESP32 GPIO & Reset
- DS: DotStar Interface
- SI: Servo Interface

NOTE that as of now, the ESP32 Reset and ESP32 GPIO functional groups have been merged.
Ditto of the 5V power and DotStar Interface FGs.

GeorgesOatesLarsen, 2020-10-11:
I will use a two-step process. First, I will fix any components that don't align with the new system (ignoring those that simply have outdated FG codes). Then, I will use one of my old scripts to do a mass re-numbering and re-naming, including automatically updating old FG codes to new FG codes.

I am committing before these changes start. Here is the commit: 879d8d4

GeorgesOatesLarsen, 2020-10-11:
Here are the renames performed in step 1:
C.EJ1
C.ES1
C.ES2
R.CD1
R.CD2
R.ED1
R.ED2
R.ES1
R.ES2
T.P1
T.P2
U$1
U$2
U$3
U$4

GeorgesOatesLarsen, 2020-10-11:
After that change, 2208e13

GeorgesOatesLarsen, 2020-10-11:
Script Used:

GeorgesOatesLarsen, 2020-10-11:
Final name changes:
NAME C.B1 C.BC1;
NAME C.B2 C.BC2;
NAME C.D1 C.DS1;
NAME C.D1* C.DS2*;
NAME C.F1 C.DS3;
NAME C.D2 C.DS4;
NAME C.D2* C.DS5*;
NAME C.F2 C.DS6;
NAME C.F3 C.DS7;
NAME C.F4 C.DS8;
NAME C.F5 C.DS9;
NAME C.F6 C.DS10;
NAME C.F7 C.DS11;
NAME C.F8 C.DS12;
NAME C.F9 C.DS13;
NAME C.F10 C.DS14;
NAME C.G1 C.ESP1;
NAME C.J1 C.VI1;
NAME C.J1* C.VI2*;
NAME C.J2 C.VI3;
NAME C.J3 C.VI4;
NAME C.L1 C.BI1;
NAME C.L2 C.BI2;
NAME C.M1 C.EC1;
NAME C.M2 C.EC2;
NAME C.M3 C.EC3;
NAME C.M4 C.EC4;
NAME C.M5 C.EC5;
NAME C.M6 C.EC6;
NAME C.M7 C.EC7;
NAME C.P1 C.USB1;
NAME C.P2 C.USB2;
NAME C.P3 C.USB3;
NAME C.P4 C.USB4;
NAME C.S1 C.SI1;
NAME C.S1* C.SI2*;
NAME C.S2* C.SI3*;
NAME C.Y1 C.YY1;
NAME C.Y2 C.YY2;
NAME C.Y3 C.YY3;
NAME C.Y4 C.YY4;
NAME C.Z1 C.ZZ1;
NAME C.Z2 C.ZZ2;
NAME C.Z3 C.ZZ3;
NAME C.Z4 C.ZZ4;
NAME C.Z5 C.ZZ5;
NAME C.Z6 C.ZZ6;
NAME D.J1 D.VI1;
NAME D.P1 D.USB1;
NAME D.Z1 D.ZZ1;
NAME F.D1 F.DS1;
NAME L.B90 L.BC1;
NAME L.F1 L.DS1;
NAME L.Z1 L.ZZ1;
NAME Q.F1 Q.DS1;
NAME Q.F2 Q.DS2;
NAME Q.J1 Q.VI1;
NAME Q.K1 Q.ESP1;
NAME Q.L1 Q.BI1;
NAME Q.L2 Q.BI2;
NAME Q.L4 Q.BI3;
NAME Q.L5 Q.BI4;
NAME Q.P98 Q.USB1;
NAME Q.P99 Q.USB2;
NAME Q.Y90 Q.YY1;
NAME Q.Y91 Q.YY2;
NAME Q.Z1 Q.ZZ1;
NAME Q.Z2 Q.ZZ2;
NAME Q.Z3 Q.ZZ3;
NAME R.B1 R.BC1;
NAME R.B2 R.BC2;
NAME R.B3 R.BC3;
NAME R.B4 R.BC4;
NAME R.B5 R.BC5;
NAME R.B6 R.BC6;
NAME R.D1* R.DS1*;
NAME R.D2* R.DS2*;
NAME R.F2 R.DS3;
NAME R.F3 R.DS4;
NAME R.F4 R.DS5;
NAME R.J1 R.VI1;
NAME R.J2 R.VI2;
NAME R.J3 R.VI3;
NAME R.J4 R.VI4;
NAME R.J5 R.VI5;
NAME R.K1 R.ESP1;
NAME R.K2 R.ESP2;
NAME R.L1 R.BI1;
NAME R.L2 R.BI2;
NAME R.L3 R.BI3;
NAME R.L4 R.BI4;
NAME R.L6 R.BI5;
NAME R.L7 R.BI6;
NAME R.L8 R.BI7;
NAME R.M1 R.EC1;
NAME R.M2 R.EC2;
NAME R.M3 R.EC3;
NAME R.M4 R.EC4;
NAME R.P1 R.USB1;
NAME R.P2 R.USB2;
NAME R.P3 R.USB3;
NAME R.P4 R.USB4;
NAME R.P5 R.USB5;
NAME R.S1* R.SI1*;
NAME R.S2* R.SI2*;
NAME SJ.K1 SJ.VI1;
NAME SJ.K2 SJ.VI2;
NAME TP.B1 TP.USB1;
NAME TP.F1 TP.USB2;
NAME TP.J1 TP.USB3;
NAME TP.M1 TP.USB4;
NAME TP.P1 TP.USB5;
NAME TP.Z1 TP.USB6;
NAME TP.F2 TP.USB7;
NAME TP.J2 TP.USB8;
NAME TP.L2 TP.USB9;
NAME TP.M2 TP.USB10;
NAME TP.P2 TP.USB11;
NAME TP.Z2 TP.USB12;
NAME TP.F3 TP.USB13;
NAME TP.P3 TP.USB14;
NAME TP.F4 TP.USB15;
NAME TP.P4 TP.USB16;
NAME TP.P5 TP.USB17;
NAME U.B90 U.BC1;
NAME U.D1 U.DS1;
NAME U.F1 U.DS2;
NAME U.G1 U.ESP1;
NAME U.M1 U.EC1;
NAME U.P1 U.USB1;
NAME U.Y1 U.YY1;
NAME U.Z1 U.ZZ1;
NAME X.D1 X.DS1;
NAME X.F1 X.DS2;
NAME X.G1 X.ESP1;
NAME X.K1 X.ESP2;
NAME X.J1 X.VI1;
NAME X.L1 X.BI1;
NAME X.L2 X.BI2;
NAME X.S1 X.SI1;
NAME X.S2 X.SI2;
NAME X.S3 X.SI3;

GeorgesOatesLarsen, 2020-10-11:
6f8f03f

Closed 2020-10-11.

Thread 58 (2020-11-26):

MKII Rev C Prototype Testing Issues and Observations

petermccloud, 2020-11-26:
Issues found during testing
1. **Power Management Status** - USING_BAT and USING_ENG appear to be switched? Verified that the correct pins are being used from the schematic.
- **No Power** - USING_BAT=0, USING_ENG=0
- **Batteries Connected** - USING_BAT=0, USING_ENG=1
- **Vraw Only Connected** - USING_BAT=1, USING_ENG=0

2. **Battery 2 Voltage** - When both batteries are disconnected, but power is applied to VRAW, battery 2 voltage appears to have a battery?

- BAT_EN=1 and ENG_EN=1
  - **Bat 2 only** - Vraw: 430mV Bat 1: 245mV Bat 2: 1363mV
  - **Bat 1 & 2** Vraw: 430mV Bat 1: 3737mV Bat 2: 4377mV
  - **Vraw only**  Vraw: 7514mV Bat 1: 245mV Bat 2: 4377mV

- BAT_EN=1 and ENG_EN=0
  - **Bat 2 only** Same
  - **Bat 1 only** Same
  - **Vraw only** 7536mV Bat 1: 245mV Bat 2: 2122mV

Other Observations
- Vraw voltage decays slowly after disconnect - Just something to be aware of for health checking

GeorgesOatesLarsen, 2021-01-19:
Closed -- all observed issues have been confirmed to be caused by fabrication issues -- Revision D has updated to accommodate this

Closed 2021-01-19.

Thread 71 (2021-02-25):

DUT4 Testing Logs

GeorgesOatesLarsen, 2021-02-25:
Forgive me, looks like I've lost my log for DUT3, and previous DUTs (there were more than 2) I don't think I have logs for at all.

I',m going to start writing test logs directly as github issues.

DUT4 looked PERFECT after soldering, except for weird patterning on the low temp side. Still thinking about that one.

Connects to USB and programmed with zero issues.

Unfortunately, DUT4 draws 0.4A when on vehicle power. DUT3 shows 0.06A. This suggests a short somewhere.

Working to diagnose.

High heat observed on U.YY1, the merge controller.

Ah, this completely my fault... I... put the component on backwards... Nice...

Simply reversing the component now yields 0.06A. Clearly just a mistake on my behalf.

GeorgesOatesLarsen, 2021-02-25:
On 7.4V to battery power, DZZ1 shows green,

GeorgesOatesLarsen, 2021-02-25:
When on Vehicle power, current draw starts at 0.06A. Connecting discharged (7.48V) batteries to battery voltage shows 0.33A. Subtracting quiescent current and adjusting to current at 7.48V, this indicates 0.43A charge current is being applied to the batteries. This is well within tolerances and indicates the battery charge circuitry is functional.

GeorgesOatesLarsen, 2021-02-25:
The USB interface just completely ripped off the PCB attempting to plug in a USB port. This is a combination of stress caused by the square extensions (which I have not yet removed), and the top-layer solder appearing to be somewhat cold-jointed. Recommend raising soak temperature by 5 degrees celcius.

GeorgesOatesLarsen, 2021-02-25:
With some finagling, got a new USB port soldered on. Serial communications are working once more. Removed the rectangular extension so this doesn't happen again. Might be worth switching to a 90 degree angle USB port. Will shop around for one.

GeorgesOatesLarsen, 2021-02-25:
Side note: List of components needing zero ohm resistors: R.DS1*, R.DS2*, R.SI1*, R.SI2*

GeorgesOatesLarsen, 2021-02-25:
Strange clicking in USB and capacitor near USB. Confirmed this is mechanical. Due to USB port mechanical stress damage from earlier

GeorgesOatesLarsen, 2021-02-25:
Strangely, LED_Builtin does not blink during flash. Possibly special firmware required for this...?

GeorgesOatesLarsen, 2021-02-25:
Testing confirms that power source control is fully functional.

That makes all systems 100% functional.

All that remains is heavy load-testing. That may take a bit for me to get to.

GeorgesOatesLarsen, 2021-05-15:
Load testing log for DUT4:

Concerned by heating up of main power module. Investigate please.

We can detect anomalous power behavior by monitoring voltage across passive load.

First, flash with program enabling engine and battery power.

Flashes with no trouble BTW (after I removed the capacitor that is supposed to fix our flashing troubles -- unit refused to flash with the capacitor installed. Still no clue about all of that jazz. This is the unit that originally motivated me to investigate our flashing problems, it refused to flash AT ALL the last time I started working on load testing).

Monitor serial, provide unit with engine power (12V).

Power supply indicates 0.07A draw.

Hmm! Current jumped to 0.5A in response to lifting board. Short?

Yes, there must be an intermittent short. It will take some time to locate. System seems to at least _**survive**_ the short, so that is encouraging. I guess it is designed to be able to, 0.5A is not really an incredible amount. There should be some heating somewhere on the board. I wonder if this is what caused the heating I noticed last time? I am going to let the short persist and search for hotspots.

Ah, interesting, the onboard LED has stopped fluttering, even on exclusively USB power. D.ZZ1 lit, but with strange and intermittent brightness. Insufficient power on ESP_POWER? 3.3V present. Is ESP32 present on serial?! No?! ESP32 is warm. Is the ESP32 shorted?

Supplying 12V to engine now shows 0.15A draw. Very dim light on D.USB1. 3.3V on esp power.

I wonder if one of the output pins of the ESP32 is shorted? It seems strange that the ESP32 would just mysteriously die.

USING_BAT shows short to ground when system inactive, but USING_ENG does not.

Pin 24 shows short to ground when inactive, 1.4V when active. Probably nothing. That pin is not connected to anything on the PCB.

No passive shorts besides the USING_BAT pin.

I don't know how, but it seems likely that the ESP32 is dead or at the very least extremely unhappy. I will attempt to remove it.

Wow. Got it removed. It was ugly AF, and it appears a transistor got swept up in the hot air and affixed itself to a capacitor, but I did it. Short is gone. Adding new ESP32 deemed a waste of time cannot use board preheater due to low temperature reverse side making the thermal pad on the ESP32 impossible to solder. Any resulting prototype would have a defunct thermal pad on the ESP32 which is a risk.

GeorgesOatesLarsen, 2021-05-15:
Okay, apparently I messed up -- DUT4 apparently passed load testing earlier, but I failed to write that here. So the strange behavior seen in the above comment must have been due to the modifications I made attempting to deal with flashing issues. Ugh. So in essence I killed DUT4, which was 100% functional, chasing a white whale. Nice.

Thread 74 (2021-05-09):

Flashing Inconsistencies

GeorgesOatesLarsen, 2021-05-09:
Prototypes have been displaying sporadic refusal to flash.

Behavior is inconsistent on the order of weeks or months, but consistent on a particular day. Some days the boards work fine. Some days, they do not ("Invalid head of packet" is the typical esptool error). Possibly caused by floating charge on ??? pin. Expected behavior and best practices are poorly documented, so it is difficult to pinpoint an exact cause.

The basic reset/reprogram transistor pair (the "esptool circuit") is correctly implemented. However, detailed testing on scope (on poor-performance days) shows extremely unstable behavior (strange oscillation, rather than expected flatline high/low reset signals) on RESET/BOOTMODE. However, this observation is extremely inconsistent. Attempts to recreate it after adding a capacitor and removing it have failed. This all suggests, again, that the cause might be a floating pin.

There are two oft-cited solutions to this problem:

1. Hidden in the implementation notes for SD card reading published Espressif themselves is the suggestion to short  to the RESET signal.
https://docs.espressif.com/projects/esp-idf/en/latest/esp32/api-reference/peripherals/sd_pullup_requirements.html
> When the GPIO2 pin is pulled high in accordance with the SD pull-up requirements, you cannot enter Download mode because. GPIO2 is a bootstrapping pin which in this case must be pulled low. For boards that require shorting the GPIO0 and GPIO2 pins with a jumper, put the jumper in place, and the auto-reset circuit will pull GPIO2 low along with GPIO0 before entering Download mode. For boards with components attached to their GPIO2 pin (such as pull-down resistors and/or LEDs), check the schematic of your development board for anything connected to GPIO2.

2. Some sources indicate that a capacitor to ground on the RESET signal is helpful.
https://pcbartists.com/design/esp32-cp2102-programmer-schematic/
https://github.com/espressif/esptool/wiki/ESP32-Boot-Mode-Selection
> Some third party ESP32 development boards use an automatic reset circuit for EN & GPIO pins, but don't add a capacitor on the EN pin. This results in unreliable automatic reset, especially on Windows. Adding a 1uF (or higher) value capacitor between EN pin and GND may make automatic reset more reliable.

Neither solution, as of current revision, is implemented on EVPR. The capacitor solution appears to be implemented by Adafruit. Confoundingly, adding this capacitor has zero effect on the outcome of flashing. However, the way in which I was forced to add the capacitor meant it was far away from the ESP32. Potentially, a closer landing pad is necessary for it to work.

See Adafruit feather schematic here:
https://cdn-learn.adafruit.com/assets/assets/000/041/630/original/feather_schem.png?1494449413

Suggestion 1., shorting I02 to BOOTMODE signal **_DID_** immediately fix the problem and yielded very reliable flashing. However, even more confoundingly, Adafruit implementation leaves IO2 floating, suggesting that it is possible to implement ESP32WROOM without this short. Why does our board need it? Does Adafruit have a custom bootloader that eliminates this issue?

Some sources suggest pullup on EN/RESET, which we do have:
https://www.esp32.com/viewtopic.php?t=11913

Same source suggests that early CP2102N chips may have a power-on reset issue? Check date code -- 1639 or later should suffice. Current date code is 2036, so this is not our problem.
https://www.silabs.com/documents/public/pcns/PCN-1611215-CP2102N-Datasheet-and-Errata-Update.pdf

Same source also suggests a capacitor from EN/RESET to **_5V_**, which is not something I have tried. This is not implemented by the adafruit feather module.

Source here suggests both capacitor from EN to ground and pullup on EN:
https://www.reddit.com/r/esp32/comments/i90hx1/autoprogramming_circuit_not_working/

Some boot mode selection documentation by espressif:
https://github.com/espressif/esptool/wiki/ESP32-Boot-Mode-Selection

Could this have anything to do with IO12, mentioned [here](https://docs.espressif.com/projects/esp-idf/en/latest/esp32/api-reference/peripherals/sd_pullup_requirements.html) and [here](
https://github.com/espressif/esptool/wiki/ESP32-Boot-Mode-Selection)? We do have DS_CLK on IO12. But that is directly connected to the SN74AHCT. Is it possible this is some how driving IO12 high?

Overall, it seems wise to add a closed solder jumper from IO2 to IO0. Consider adding landing pads for capacitors between RESET and both GND/5V. Consider transplanting adafruit ESP32 module to test for bootloader differences.

GeorgesOatesLarsen, 2021-05-10:
So that short from IO2 to IO0 actually prevents the reset button from working. We need a different solution.

GeorgesOatesLarsen, 2021-07-01:
I am leaving this arguably duplicate issue open for now. I have a strong suspicion that we've been dealing with multiple issues. One, a design problem due to the lack of that capacitor. The other due to process issues leading to the unpredictably faulty flashing observed here. I think the process issues in the boards I reference above meant that even when I fixed the capacitor issue, I still saw problems flashing. However, DUT6 from #76 is extremely consistent. I am hoping to repeat some of the ideas here and actually get waveforms for them so that I can conclude finally on what could be causing our flashing issues. This issue will probably be closed no matter what the results are, but I want to get certainty first.

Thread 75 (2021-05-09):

Deep Sleep Considerations

GeorgesOatesLarsen, 2021-05-09:
Firstly, there is the silly placement of the ESP32 power LED. This will bleed our power. Remove it. #73

See documentation on sleep modes for ESP32:
https://docs.espressif.com/projects/esp-idf/en/latest/esp32/api-reference/system/sleep_modes.html

We are namely interested in esp32 deep sleep. Wakeup can be triggered by any of the RTC_GPIO pins. It is unclear why these are named after the Real Time Clock, but in general RTC_GPIO are the only pins accessible in deep sleep or deeper.

See:
https://docs.espressif.com/projects/esp-idf/en/latest/esp32/api-reference/peripherals/gpio.html

While I'm at it, here are the big three datasheets from esp32:
https://www.espressif.com/sites/default/files/documentation/esp32_hardware_design_guidelines_en.pdf
https://www.espressif.com/sites/default/files/documentation/esp32_technical_reference_manual_en.pdf
https://www.espressif.com/sites/default/files/documentation/esp32_datasheet_en.pdf

And for the WROOM:
https://www.espressif.com/sites/default/files/documentation/esp32-wroom-32_datasheet_en.pdf

Somewhere in those four documents lies documentation on what the RTC-GPIO pins actually are.

GeorgesOatesLarsen, 2021-05-09:
Ah, yes, section 2.2 of the WROOM database. Pin definitions. Anything labeled "RTC_GPIOX", such as "RTC_GPIO0" or "RTC_GPIO1", so forth. Those are our RTC GPIO pins.

GeorgesOatesLarsen, 2021-05-09:
We are interested in awakening on RAWSENSE. This is IO34, pin 6. Fortunately for us, this is, in fact, an RTC_GPIO. It is RTC_GPIO4.

We are interested in keeping our BAT_EN signal low. Currently, BAT_EN lives on IO21, pin 33. Unfortunately, this is _not_ an RTC GPIO.

We have two options:

1. Relocate BAT_EN to a GPIO pin that is RTC_GPIO.
2. Some sources suggest that a special setting can keep the main GPIO active during deep sleep.

Namely:
```c
gpio_hold_en(GPIO_NUM_25);
gpio_deep_sleep_hold_en();
```
https://github.com/espressif/arduino-esp32/issues/2712

Need to test what the power implications of that second option are. Will test now.

GeorgesOatesLarsen, 2021-05-09:
The ESP-IDF function for wakeup is esp_sleep_enable_ext0_wakeup. We want ext0 since we want only a single pin to wake us up. Documented here:
https://docs.espressif.com/projects/esp-idf/en/latest/esp32/api-reference/system/sleep_modes.html

Yes, wake from sleep functions perfectly:
```C
void setup() {
  Serial.begin(115200);
  Serial.println("BOOT!");
  pinMode(GPIO_NUM_21,OUTPUT);
  digitalWrite(GPIO_NUM_21, LOW);
  esp_sleep_enable_ext0_wakeup((gpio_num_t) 34, HIGH);
}

void loop() {
  for (int i = 0; i < 5; i++) {
    Serial.println("Going to sleep soon.");
    delay(1000);
  }
  gpio_hold_en((gpio_num_t) 21);
  gpio_deep_sleep_hold_en();
  delay(1000);
  esp_deep_sleep_start();
  Serial.println("This never prints, since deep sleep resets memory.");
}
```

GeorgesOatesLarsen, 2021-05-10:
Now I just need to characterize the power draw. I don't have very sensitive current measuring capabilities, but I'll do my best. I will deliver batteries to the battery pins, passed through voltmeter.

Yeeeeaaah, my multimeter can't even measure the current when in deep sleep mode. It's like, on the order of less than a microamp. I am pretty sure a full charge will last years with this current consumption,

GeorgesOatesLarsen, 2021-05-10:
Just as a final summary:

Near start-up, call:
```C
  esp_sleep_enable_ext0_wakeup((gpio_num_t) 34, HIGH);
```
to enable wakeup triggered by rising engine power.

To go into deep sleep:
Bring GPIO21 to LOW (this disables use of the battery)

Then, call:

```C
gpio_hold_en((gpio_num_t) 21);
gpio_deep_sleep_hold_en();```

Then wait a few hundred milliseconds for good measure.

Then, call:
```C
esp_deep_sleep_start();```

And as of that moment, the ESP32 will enter deep sleep.

Please note that deep sleep totally wipes ESP32 memory, so no variable values or anything of that sort will be retained after waking up. Waking up from deep sleep will be akin to experiencing a reset. So, if there is anything nontransient you want to return after deep sleep, you'll need to use the onboard flash to save it.

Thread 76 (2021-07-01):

USB Flashing Issues

GeorgesOatesLarsen, 2021-07-01:
Okay, we definitely have some kind of a consistent flaw that produces inconsistently bad flashing. DUT6 seems to be particularly stable in its behavior, stable enough for me to attempt a characterization, and it definitely displays incorrect behavior.

This issue will be a journal for the debugging process and will contain the data I collect. Hoping to get to the bottom of this.

GeorgesOatesLarsen, 2021-07-01:
Let's start with what I've done so far:

First of all, the board shows zero signs of any problems with the USB to serial chip, or the 3.3V power path, or the ESP32 itself. No abnormal heating, I can talk to the USB serial itself just fine with zero issues, and the ESP32 is reading 3.3V on the appropriate pin. By all accounts the thing should be working. The issue is almost certainly that the autoreset circuitry is failing to place the ESP32 bootloader into download mode.

I have been able to get very consistent waveforms of the four nets involved with entering into download mode: DTR/RTS/RST/IO0. I've taken these waveforms for both DUT6 and  a modified ESP32 feather, and this confirms that something is very wrong with the autoreset circuitry. Deeply analyzing these waveforms may reveal the kind of electrical issue we are dealing with.

First, a simple screenshot (for now) of the data, which was triggered on a sufficiently long low pulse observation on IO0. I manually corrected some misalignment (due to an interesting discrepancy I will discuss later), but the correcting offset turned out to be 0.13 seconds, or thereabouts. (That is, the DUT6 data needs to have its time values shifted forward in time by 0.13 seconds).

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

GeorgesOatesLarsen, 2021-07-01:
There is a lot to take in here, I will do my best to summarize my thoughts. It is helpful, first, to start by trying to understand the feather on its own. Here is a combined graph of its activity:

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

GeorgesOatesLarsen, 2021-07-01:
So, what is going on here? Well, RTS and DTR drive the entire process; they remain high (AFAICT) up until the point at which esptool wants to enter the download mode. Actually, real quick, here is the source code responsible for doing this:

```py
def bootloader_reset(self, esp32r0_delay=False, usb_jtag_serial=False):
        """ Issue a reset-to-bootloader, with esp32r0 workaround options
        and USB-JTAG-Serial custom reset sequence option
        """
        # RTS = either CH_PD/EN or nRESET (both active low = chip in reset)
        # DTR = GPIO0 (active low = boot to flasher)
        #
        # DTR & RTS are active low signals,
        # ie True = pin @ 0V, False = pin @ VCC.
        if usb_jtag_serial:
            # Custom reset sequence, which is required when the device
            # is connecting via its USB-JTAG-Serial peripheral
            self._setRTS(False)
            self._setDTR(False)  # Idle
            time.sleep(0.1)
            self._setDTR(True)  # Set IO0
            self._setRTS(False)
            time.sleep(0.1)
            self._setRTS(True)  # Reset. Note dtr/rts calls inverted so we go through (1,1) instead of (0,0)
            self._setDTR(False)
            self._setRTS(True)  # Extra RTS set for RTS as Windows only propagates DTR on RTS setting
            time.sleep(0.1)
            self._setDTR(False)
            self._setRTS(False)
        else:
            self._setDTR(False)  # IO0=HIGH
            self._setRTS(True)   # EN=LOW, chip in reset
            time.sleep(0.1)
            if esp32r0_delay:
                # Some chips are more likely to trigger the esp32r0
                # watchdog reset silicon bug if they're held with EN=LOW
                # for a longer period
                time.sleep(1.2)
            self._setDTR(True)   # IO0=LOW
            self._setRTS(False)  # EN=HIGH, chip out of reset
            if esp32r0_delay:
                # Sleep longer after reset.
                # This workaround only works on revision 0 ESP32 chips,
                # it exploits a silicon bug spurious watchdog reset.
                time.sleep(0.4)  # allow watchdog reset to occur
            time.sleep(0.05)
            self._setDTR(False)  # IO0=HIGH, done```

GeorgesOatesLarsen, 2021-07-01:
I've removed the branches of code that are unused. Let's walk through both the script and the waveform simultaneously.

Like I said, RTS and DTR drive the entire process; those are the pins that esptool has direct access to. Lining up the code to the waveform is a little difficult, but my understanding is this is what happens:

When not in use, RTS and DTR are pulled up. When esptool boots, I **_suspect_** that both RTS and DTR default to the low state. That is, the very act of establishing control over them resets them to low. Hence why we see both go low at the same time, even though no point in the code calls for this.

Notice, also, that there is a slight delay on them. This causes DTR to be high just a little longer than RTS, and that causes RST to be shorted to zero very briefly, which we see as the first dip on RST. Almost immediately RST starts recovering, but is slowed down by the hefty capacitor included by Adafruit.

Now, another bit of guessing. I THINK in this case setting DTR high actually indicates a low voltage on our graph, since DTR and RTS are active low. The sparse comments do not specify, and I did not feel inclined to navigate through the rabbit hole of dependencies to find out. But it would match with our patterns.

So, our first act is to set DTR to false, which brings DTR high. We also set RTS to true, bringing it low, but it was already low by default.

Then we wait 0.1 seconds, and swap their values -- a transition we see on the graphs as well.

At the very end, we set DTR to false, which brings it high, again reflected on the graph.

I'm taking the fact that my interpretation of this code yields an expectation that perfectly matches the reality reflected in the graph as an indicator that my interpretations are valid.

GeorgesOatesLarsen, 2021-07-01:
Ultimately DTR and RTS are just control signals. What we really care about is what happens with IO0 and RST. We want to bring both IO0 and RST low (causing an active reset state), and then we want RST to go high SIGNIFICANTLY BEFORE IO0 goes high. By raising RST before IO0, we wake the ESP32 while keeping IO0 low, which is precisely what indicates to the ESP32 that it should enter download mode.

The importance of the capacitor in the design is a matter of active debate. Obviously, none of this is even acknowledged by Espressif even though this circuit has become kind of a standard with anything implementing ESP32. Quite candidly, I don't fully understand how the dual-BJT circuit works even in ideal conditions. For instance, I don't see a reason that IO0 should go low when RTS, DTR, and RST are briefly brought low. IO0 is pulled up internally, and in that situation I wouldn't think there is any conduction. Very strange. Plus, the whole spurious reset directly before the actual, genuine reset attempt is very odd. Never seen anyone talk about that at all.
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
GeorgesOatesLarsen, 2021-07-01:
Scope completely disconnected: Upload fail
CH1 ground connected: Upload Fail
CH1gnd + CH1 to IO0: Upload succeeds after one failure
CH1gnd + CH1 to IO0, CH2 to RST: Upload succeeds after several failures
All connections made: Immediate success

GeorgesOatesLarsen, 2021-07-01:
Closest I have is 20pF. That'll do.

Adding the four capacitors did not stabilize the circuit. Total upload failure.

Grounding to oscilloscope AND adding bodge had no effect.

Scoping with bodge caps also results in total failure.

Scoping with bodge caps removed resulted in immediate success.

So, 20pF caps to all channels is NOT the solution we are looking for....

I am wondering if there is a weak pulldown effect caused by the probes?

GeorgesOatesLarsen, 2021-07-01:
Yes, there is a weak pull-down effect on all channels. I need to scope it properly to measure the equivalent resistance...

GeorgesOatesLarsen, 2021-07-01:
Observing discharge of approximately 0.1pf capacitor, we see:

V_0: 3.2V
V_1: 1.12V
time delta: 128.8 ms

1.12V = 3.2V e^(-128.8ms/(RC)

-128.8ms/(ln(1.12/3.2) * 0.1uF) = R

About 1.2 megaohms. Which, I mean, okay yeah, that's pretty much in line with the impedance listed on the datasheet, lol. I guess I'll try a network of 1megaohm resistors and see what that does.

GeorgesOatesLarsen, 2021-07-01:
With 1M network, flashing still fails. Ugh.

Fascinatingly, however, adding the 1M network, and connecting the device to GND of the oscilloscope, but NOT connecting probes results in immediate flash success.

Let me try connecting that missing capacitor again.

It actually stops working, interestingly.

Disconnecting it returns circuit to immediate success.

So, we have established that, somehow, the addition of a path to ground via the oscilloscope, AND the addition of 1M pulldowns on all channels stabilizes the programming process.

The big question is: Why the hell?

I need to try a variety of grounding positions for the oscilloscope to see if perhaps we have a bad ground plane?

GeorgesOatesLarsen, 2021-07-01:
Oddly enough, the device is actually functioning fairly well now without being grounded via the oscilloscope. Strange. More testing to follow.

GeorgesOatesLarsen, 2021-07-01:
Removing and re-adding power seems to have suddenly broken the ability of the system to flash. I am going to try probing to see what happens, even grounding is not returning it to function.

Still failing, even when probed. Interesting.

Okay. I think the ground connection to my resistor bodge network was bad.

I am getting really inconsistent flashing behavior. It seems like a coin toss whether the system will flash. When it decides to flash, it tends to do that quite a few times in a row. Whenever I disconnect and reconnect power, it seems to return to being unable to flash. I have gotten it to flash reliably when not connected to the scope, but this doesn't last through a power reset. Seriously wondering what is going on here.

I have a bit of a hunch that we need a capacitor or a resistor to prebias the BJT circuit. Thing is, I haven't once had a successful flash with the big beefy capacitor connected. But then again, maybe that is all coincidence.

So, I think my next goal is going to be to try to get a waveform with the capacitor on. That would be nice to see.

GeorgesOatesLarsen, 2021-07-01:
Okay, I am tempted to write a modified version of ESPtool that produces simple square waves on the DTR and RTS channels because this is proving to be rather unreliable. The failure mode seems to be short pulses at about the spacing I might expect value changes for DTR and RTS. Are we somehow dealing with a bizarre form of AC coupling? I don't rightly know.

It's also worth checking the differences between CP2102N and CP2104 in terms of DTR/RTS electrical characteristics. Might be some differences? CP2104N can sink up to 100mA through any IO pin. Ditto on CP2012N. Doesn't seem likely this is due to some kind of max current issue or such...

GeorgesOatesLarsen, 2021-07-01:
I wonder if the 3.3V supply on CP2102N is slightly different than the 3.3V supply for ESP32, and this is somehow creating slight differences in voltage that prevent the BJT circuit from operating correctly? I think soldering the two together is in order.

GeorgesOatesLarsen, 2021-07-01:
No luck. But I will try to get a waveform.

Agh. Okay, I am ralizing now that if VREGIN is shorted to VDD it needs to be disconnected from VBUS. Yikes. Might have damaged the whole thing. We'll see.

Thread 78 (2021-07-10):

DUT6/DUT7 Testing Log

GeorgesOatesLarsen, 2021-07-10:
DUT6 is stuck in programming mode due to an apparently irreparable short of the BOOTMODE pin to GND. It programs just fine, but literally cannot execute its program.

It is unclear how this short is even possible, but I did find some slight misalignment in the ESP32 package, as well as a via to GND that was perhaps too close to the BOOTMODE pin.

It is impossible for me to say which of these two issues is the cause of our short just yet. Our best bet would be to use a manual mill to cut the trace to BOOTMODE as close to the ESP32 as possible, and observe whether the short still exists. I cannot do that here.

However, I have already corrected the misalignment in the package, as well as greatly increased the margin between under-ESP32 vias and their pins (except where a short to the corresponding pin is intentional). Hopefully both of these issues will prevent this problem from occurring in the future.

I was able to remove the autoreset circuitry and manually program DUT7, so DUT7 is able to be load tested. Results here soon.

GeorgesOatesLarsen, 2021-07-10:
DUT7 draws 0.4A on 12V, and thermal pad gets hot very fast. Similar behavior observed on USB. Not even booting in programming mode rectifies. DUT6 has no such issue. Neither does DUT5

So DUT6 is stuck in programming mode, and DUT7 can be programmed (and communicated with) just fine, but actively tries to set itself on fire.

***Both*** problems are indicative of some kind of short with the ESP32.

it is, once again, possible this was caused by our misaligned ESP32 package. I'm not sure how we went this long without seeing this program, though.

YIKES. 3v3 shows an anomalous short to GND. Furthermore, it turns out I can no longer contact the ESP32. What happened?! I was able to program it and get serial data just fine. I expose it to 12V, and now I cannot? I will perform the same test on DUT5. It cannot be programmed, but perhaps it will also immediately stop functioning after exposure to 12V.

No heat on thermal pad with USB power...

High current NOT drawn when on 12V.

I will see if I can bypass the autoreset for DUT5. I am realizing it may have been too early to give up on it just yet.

No luck.

I will need to think about this. The shorts we are getting, seemingly at random, and in response to no stimulus at all, are very perplexing.

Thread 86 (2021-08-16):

DUT9 Testing Log (and some notes on STILTS)

GeorgesOatesLarsen, 2021-08-16:
DUT9 is first proper prototype of Rev E.

There was a Rev E prototype that I did not end up assigning a DUT number due to its relative strangeness (It's the prototype on stilts -- frankly, I want that prototype in a display case one day). Gonna refer to that as STILTS as opposed to a DUTX.

STILTS ended up being nearly fully functional (no abnormalities detected at all except for one). The one abnormality was the inability to disable battery power source in software. Likely related to a misaligned transistor. Fingers crossed DUT9 suffers no such issue.

DUT9, as with STILTS, has 100% functional serial, no fiddling required. This increased my confidence that I narrowed in on the underlying circuitry causing the intermittent serial unreliability we have been plagued with for the past year.

(For the curious, the problem, I am pretty sure, is that the builtin 3.3V supply on the usb interface was NOT disabled, and ended up giving a slightly different voltage than the 3.3V supply for the ESP32. This is 100$ A-OK for the actual serial communications, the voltages are close enough. But the autoreset circuitry is basically a BJT implementation of a XOR gate, and exposing it to those slightly different voltages, according to my theory, caused it to behave in an unexpected fashion. On the latest revisions, the USB interface 3.3V supply is properly disabled, and I haven't had a single issue flashing since.)

DUT9 also draws 0.06A quiescent current when on engine power which is right in line with what I observed for STILTS. (0.07A). his is kind of a high quiescent. I have a hard time accounting for it fully, but who knows. We do have a lot of devices drawing tiny amounts of current from it, and at such low currents, the main converter will have a horrendous efficiency. Certainly, it seems consistent, and there is no majorly abnormal heating -- the majority of the heating is with the main converter, which lines up nicely with the inefficiency theory.

Serial and programming remain 100% functional, even when on engine power. Shorts between the serial lines and the adjacent battery status report pins have caused issues in the past, so this is another indicator of good health.

Also, I am noting that our ESP32 has NOT spontaneously combusted yet -- this one is NOT on stilts, so this is a sign we MAY have solved whatever issue was causing that -- either inopportune via placement, or just too much thermal pad solder. Or both! Not sure. Then again, we only even had this issue on the last three prototypes from revision D, so it is hard to gauge the consistency of the problem, as well as whether or not it is permanently fixed. Time will tell, but it's excellent that we are thus far not having any issues with this. By this point, all three of the most recent rev D prototypes had self-destructed.

Flashing the power test program, now, to verify working of builtin LED and to begin testing power management systems.

Compiled and flashed with zero issue. Receiving test data via serial. Very, VERY good sign. We have not made it this far on a DUT in quite a while. I would like to reiterate the fact that autoreset is working flawlessly now.

Actual test data seems reasonable. The battery/engine usage statuses seem a bit odd at times, for instance:

```
CHGOK: 1, ACOK: 0
TUE: Yes, TUB: No
UE: No, UB: No
```

Here indicating that we are attempting to use engine, but NO power source is being used. I am willing to attribute this to the absolutely miniscule amount of current actually being drawn post-converter. These outputs will make more sense when we load test.

It does, however, make sense to make some early voltage measurements to ensure the power enable/disable is actually operating.

Very promising results, alternation between ~1V and 8.4V. Actually, this is way better than seen even on STILTS, suggesting that STILTS may have had a downright damaged power management transistor, rather than misaligned.

We are ready to perform battery testing now.

GeorgesOatesLarsen, 2021-08-16:
Firstly, note CHGOK:1, ACOK:0 in the above, which is the correct response to a lack of battery.

Tiny amount of current when on simulated battery, the status indicator blinks in accordance with program. Together these indicate that the battery power chain is very healthy!

We need to test serial while on battery, and then we need to also test the charge circuitry, as well as power management on battery side, but this is an exceptionally good sign.

GeorgesOatesLarsen, 2021-08-16:
Serial remains very much alive!

Very, very good.

Alternating between 7.4V and ~1V on sys_pow, as expected. Whatever plagues STILTS, it does NOT plague DUT9. Very, very, very good. Now to test charging.

GeorgesOatesLarsen, 2021-08-16:
Status LED indicates correct function when on true battery. Serial is also remaining functional.

Note that the batteries are under-charged!

Providing both batteries AND engine power, 0.32A is consumed. Subtracting 0.05 quiescent, and multiplying by conversion factor between 12V and ~7V, we obtain 0.44A, which is right around the target voltage -- So charge circuitry DOES work. Also, CHGOK and ACOK are both zero, indicating charge mode is active.

GeorgesOatesLarsen, 2021-08-16:
Now performing a 30 minute charge test. Starting voltage is 7.2V.

GeorgesOatesLarsen, 2021-08-16:
7.7 volts in the end! Was still showing full current, but the terminal charge voltage is 8.2V, so that makes sense.

Battery charging works just fine.

That means the entire power path is functional. Time for load tests, now. Crimping on the resistive load...

GeorgesOatesLarsen, 2021-08-16:
Load test from engine power shows alternation between 3A and 0.07A, indicating perfect function of power cutoff for engine side... Will repeat for battery side momentarily.

voltage across load resistors is alternating between 8.0V and 0V. 0.4Vdrop somewhere in the system... Gonna run for some time, try to find it, and make note of any heating.

Looks like most of the vdrop is in the connector, OR, in the wire I am using to connect to it.

The wire has extremely low vdrop. Interestingly, it is measurable, but very low.

The connector is where most of our vdrop is occurring. It's about 0.4V. At 3A, that's about 1.2 watts of lost power. Not sure if that is really in spec or not, will check later.

GeorgesOatesLarsen, 2021-08-16:
Oh, and there was no major heating observed, not even in the connector, although 1 W is not much in terms of heating for a connector of that size.

On simulated battery, alternating between 0A and 3.77A.

Also, worth note that serial still works; did not try this for the other power test, but we'll get there with the final load testing round.

Serial output data:

```

CHGOK: 1, ACOK: 1
TUE: No, TUB: No
UE: No, UB: No

CHGOK: 1, ACOK: 1
TUE: Yes, TUB: No
UE: No, UB: No

CHGOK: 1, ACOK: 1
TUE: No, TUB: Yes
UE: No, UB: Yes
I am alive!
1

CHGOK: 1, ACOK: 1
TUE: Yes, TUB: Yes
UE: No, UB: Yes

CHGOK: 1, ACOK: 1
TUE: No, TUB: No
UE: No, UB: No
```

This makes perfect sense, and finally lines up with expectations now that there is a significant load on the system.

Voltage across resistors is alternating between 0 and 7.4V, which indicates vdrop in the connector and PERFECT operation of power control system. It gets a 100% pass at this point.

Only thing left to do is to verify nothing is overheating...

lol, the board is pretty cool, actually. This makes sense; the battery power path is more or less direct. No conversions take place. But the place where this can go wrong are the two pairs of power control mosfets, which are both literally cool to the touch, so I am going to say this is a pass with flying colors.

Final test is to ensure that when both batteries and engine are present, engine is prioritized over batteries due to the higher input voltage. This helps the batteries charge while they are not being used.

GeorgesOatesLarsen, 2021-08-16:
Operating on true batteries. I have no current measurement, but serial output indicates successful use:

```

CHGOK: 1, ACOK: 1
TUE: Yes, TUB: Yes
UE: No, UB: Yes

CHGOK: 1, ACOK: 1
TUE: No, TUB: No
UE: No, UB: No

CHGOK: 1, ACOK: 1
TUE: Yes, TUB: No
UE: No, UB: No

CHGOK: 1, ACOK: 1
TUE: No, TUB: Yes
UE: No, UB: Yes
```

Also, seeing an alternating voltage across resistors between 0 and 6.7. Nice.

Now, adding engine power. This will be interesting. This is the final test before a 100% pass for all systems.

That's pretty cool, we alternate between 3.32A and 0.33A corresponding to the engine power being enabled and disabled. (The battery charger takes power from engine directly).

```
CHGOK: 0, ACOK: 0
TUE: No, TUB: Yes
UE: No, UB: Yes
I am alive!
27

CHGOK: 0, ACOK: 0
TUE: Yes, TUB: Yes
UE: Yes, UB: No

CHGOK: 0, ACOK: 0
TUE: No, TUB: No
UE: No, UB: No

CHGOK: 0, ACOK: 0
TUE: Yes, TUB: No
UE: Yes, UB: No
```

Indeed, when both engine and battery are requested, engine is prioritized. I will confirm this by taking a voltage measurement with a simplified version of the program.

GeorgesOatesLarsen, 2021-08-16:
Flashing, as per usual, went completely without a hitch.

Voltage across resistors shows 8V, indicating that, indeed, we truly are sourcing from engine. Hell yes.

Final heat check shows the circuit is warm to touch, but not overheating.

DUT9 is 100% passing all tests

GeorgesOatesLarsen, 2021-08-20:
Side note, it just dawned on me that I did not manage to label DUT9. This should be corrected at some point

GeorgesOatesLarsen, 2021-09-30:
Closing; these test logs are no longer relevant

Closed 2021-09-30.

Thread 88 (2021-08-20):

DUT10 Testing Log

GeorgesOatesLarsen, 2021-08-20:
OK! DUT10 is assembled.

Let's test it.

Flashing and serial work flawlessly as per usual. Although the USB ports for both USB interface cards is a bit fiddly, likes to drop out under stress. AFAICT, this is just the connector element itself, not the soldering or the cables. USB connectors on COTS ESP32 modules do not have this problem, although there are noticeable visual differences between those microUSB connectors and ours. I'm just thinking this is down to our part selection.

On engine power: 0.06A draw (nominal). Serial & Flash survive.  sys_pow alternating from ~1V to 8.4V
On simulated battery: 0.01A draw on 7.4V. Serial & Flash survive. sys_pow alternating from ~0.7V to 7.4V.

This indicates basic power path is fully functional.

On simulated battery, log outputs:

```
CHGOK: 1, ACOK: 1
TUE: Yes, TUB: Yes
UE: No, UB: Yes

CHGOK: 1, ACOK: 1
TUE: No, TUB: No
UE: No, UB: No

CHGOK: 1, ACOK: 1
TUE: Yes, TUB: No
UE: No, UB: No

CHGOK: 1, ACOK: 1
TUE: No, TUB: Yes
UE: No, UB: Yes
```

I'm gonna go ahead and paste a copy of the ACOK CHGOK chart from the MP2615 datasheet:

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

In this case, 1 is High Impedance, 0 is Low.

CHGOK1 ACOK1 corresponds to V_in absent, as expected, since engine power is not being provided.

On genuine battery:
Status indicator blinking. Serial survives. Sys_Pow alternating between ~0.7V and 7.5V

Serial output is:
```
CHGOK: 1, ACOK: 1
TUE: Yes, TUB: Yes
UE: No, UB: No

CHGOK: 1, ACOK: 1
TUE: No, TUB: No
UE: No, UB: No

CHGOK: 1, ACOK: 1
TUE: Yes, TUB: No
UE: No, UB: No

CHGOK: 1, ACOK: 1
TUE: No, TUB: Yes
UE: No, UB: Yes
```
Same deal.

On genuine batteries AND 12V engine:
0.33A drawn on engine. Subtracting 0.06A, multiplying by conversion factor, this is 0.43A charge current, which is within spec.

sys_pow is stepping through: 8.4V, 7.65V, 8.4V, ~1V, indicating power management operational.

Serial Output:
```
CHGOK: 0, ACOK: 0
TUE: Yes, TUB: Yes
UE: Yes, UB: No

CHGOK: 0, ACOK: 0
TUE: No, TUB: No
UE: No, UB: No

CHGOK: 0, ACOK: 0
TUE: Yes, TUB: No
UE: Yes, UB: No

CHGOK: 0, ACOK: 0
TUE: No, TUB: Yes
UE: No, UB: No
```
Indicating that charging is in progress.

Battery voltage has increased to 7.6V, indicating successful charging.

Finally, load testing must be performed. I will do a single comprehensive load test with battery and engine power connected to the full load.

Current alternates between 0.31A and 3.35A, about what are expected.

Voltage across the resistive load follows the sequence: 0V, 8.1V, 6.8V, 8.1V

This indicates there is about a 0.3V vdrop in the system somewhere... Interesting.

Voltage at the servo connector pads is 8.25V and 6.95V, so it looks like most of the vdrop is in my wires. 0.14Vdrop roughly in the wires.

This seems acceptable, but only testing on the vehicle will tell for sure.

As for device heating: The main converter does get "quite hot" -- Still cool enough to touch without being burned, but just uncomfortable. This is nominal.

Power merge dual transistor gets slightly warm, but not significantly. I measure about a 0.78 vdrop under high load.

The power control transistor gets mildly warm.

Serial remains operational at all times

Serial output is:

```
CHGOK: 0, ACOK: 0
TUE: Yes, TUB: Yes
UE: Yes, UB: No

CHGOK: 0, ACOK: 0
TUE: No, TUB: No
UE: No, UB: No

CHGOK: 0, ACOK: 0
TUE: Yes, TUB: No
UE: Yes, UB: No

CHGOK: 0, ACOK: 0
TUE: No, TUB: Yes
UE: No, UB: Yes
I am alive!
```
When targeting both engine and battery, engine is correctly selected, while the battery is charged.

When targeting neither, neither is used.

When targeting only battery or engine, the respective power source is correctly selected.

DUT10 gets a full pass!

Though I find the vdrop in our transistors concerningly high. Doesn't quite seem to add up with what is listed in the datasheet, IMO. But I will need to look a little closer at the datasheet.

GeorgesOatesLarsen, 2021-08-20:
It occurs to me that I may have missmeasured the vdrop across Q.YY1. It needs to be in a specific power mode. I will place it into engine-only mode and measure vdrop.

Ha, yep. I mis-measured. It's actually 0.06V which is ***pretty much*** in line with the datasheet (quoting about 12milliohms, which would yield an expected 0.03V drop).

Overall, pretty happy with DUT10.

GeorgesOatesLarsen, 2021-08-20:
Decided to let the charge circuitry do its thing for a while. Looks like it successfully completed a charge cycle! Current draw from engine power is back down to 0.06A.

```
CHGOK: 1, ACOK: 0
TUE: Yes, TUB: No
UE: Yes, UB: No
I am alive!
9304
```

This does, indeed, correspond to end of charge condition.

Board is nice and cool.

Terminal battery voltage is 8.3V.

I think it would make sense to do another load test, mainly focusing on the final voltages seen by the load, as well as ensuring that we are still defaulting to engine power when both sources available.

```
CHGOK: 0, ACOK: 0
TUE: Yes, TUB: Yes
UE: Yes, UB: No

CHGOK: 0, ACOK: 0
TUE: No, TUB: No
UE: No, UB: No

CHGOK: 0, ACOK: 0
TUE: Yes, TUB: No
UE: Yes, UB: No

CHGOK: 0, ACOK: 0
TUE: No, TUB: Yes
UE: No, UB: Yes
I am alive!
```

Indeed, we default to engine.

load voltage cycle: 8.1V, 7.5V, 8.1V, 0V

Battery voltages: Alternating between 7.8V and 8.2V. So, under load, dropping to 7.8V.

This means the battery is showing about 0.3V drop on both the battery and engine power.

This also means that during an emergency power kick-in, even under stall condition, servos will still receive around 7.5V assuming the batteries were fully charged. The fact that we are selecting engine power even with fully charged batteries indicates that the batteries will be able to charge.

It would be worthwhile to do some current measurements on the battery when fully charged to be 100% certain that we truly are not drawing current from the batteries.

GeorgesOatesLarsen, 2021-09-30:
Closing, no longer relevant (no issues were found here, and we are on to a new revision)

Closed 2021-09-30.

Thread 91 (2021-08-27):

Improve Low-Temperature reflow process

GeorgesOatesLarsen, 2021-08-27:
Low-Temperature reflow results are unsatisfactory. They work, but there are signs of problems. Would be good to spend some time trying to properly improve.

Possibly switch to normal solder and reverse order of soldering?

GeorgesOatesLarsen, 2021-09-02:
@petermccloud

Do we want to attempt a pass using only high-temp solder for the next round of boards, or just stick to the process used for the last batch?

GeorgesOatesLarsen, 2021-09-30:
DUT11 and DUT12 were both reflowed using exclusively high-temp solder. Zero issues!

Closed 2021-09-30.

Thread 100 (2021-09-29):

Magnet for RPM sensing

petermccloud, 2021-09-29:
Need a magnet in the brush holder for RPM sensing.

@GeorgesOatesLarsen Below is the link for the magnet I'm considering for RPM sensing. It's the same width and depth as the brushes. (1/4"x1/4") so I should have minimal issue incorporating it. If there's any potential issues you see, let me know.

https://www.mcmaster.com/5848K91/

GeorgesOatesLarsen, 2021-09-29:
The only issue I see is that it might be possible to place the magnet in the wrong direction, since it is a cube, which would render the hall effect sensor useless -- A disc magnet might be better?

@petermccloud

petermccloud, 2021-09-29:
@GeorgesOatesLarsen I think you're right about the disc shape. I can fit two of the below magnets in the brush holder.
https://www.mcmaster.com/5862K166

GeorgesOatesLarsen, 2021-09-30:
I'm not sure whether that would work very well; The magnetic pole needs to face perpendicularly to the axis of the rotor shaft. The height of those magnets makes me think you might be planning to have them parallel to the shaft?

Actually, those magnets seem pretty tiny to me, what about:
https://www.mcmaster.com/5862K141/
?

Also, I am thinking since it would be ideal to have two magnets with flipped poles, we end up having to be careful about the magnet orientation anyways. Although with disc magnets, its just important that we get the magnets facing the opposite direction as each other, whereas with cube magnets, there are a large number of other orientations that are incorrect

@petermccloud

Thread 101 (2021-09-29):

Current brush board shows signs of catastrophic wear

GeorgesOatesLarsen, 2021-09-29:
I am getting extremely inconsistent system voltage coming through the brushes on the rotor prototype that you dropped off with me, @petermccloud

Here is a picture of the tracks under a microscope:
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

That regular grid pattern is particularly concerning, as that is presumably the weave pattern of the fiberglass substrate. I think we are wearing the copper down to the substrate.

I wasn't able to get any visible sparking, but this problem is much more serious.

There is definitely some wear and tear on the in-house track you made, but it has not gotten anywhere near wearing down to the substrate like that. I don't see a fiberglass weave on that board.

This problem was creating some pretty serious power interruptions on engine-power. Enough for the engine power indicator to visibly change brightness, for the current output on my power supply to significantly change, and for an oscilloscope read I had on the track to go berserk (though I don't have any good pictures of this). We're dropping down as low as, like, 6V, at times. It's real bad.

Since we are moving away from using a brush-based tach, maybe we should just adhere a copper ring to some blank FR4? Or something similar, that would allow some raw copper to be used? Perhaps we can cut some copper sheet into a shape such that we can screw it down onto the existing brush board? Something that would let us use significantly more copper than we currently are.

petermccloud, 2021-09-29:
Wow! Thanks for digging into that!

That brush PCB has only been spun around by hand. The previous boards have been spun by the motor. I thought both the homemade brush path and the OSHPark one were both 2oz copper. I'm trying to confirm what I got from Injectorall, but the invoice doesn't list the weight. It perhaps could have been 4oz.

The easiest solution is to return to using the original copper brush path boards, but omit the tach trace. If those wear out, we can switch to solid copper.

GeorgesOatesLarsen, 2021-09-30:
Holy cow, ***that*** was just from ***hand spinning?!***

That's insane!

I thought we ordered 4oz from osh park? Or was it 2oz after all?

Either way, I kind of doubt that doubling the thickness will make much difference with osh, given what we've seen. Unless, perhaps, the gold plating is creating a softer alloy? I wonder if a run of unplated 4oz copper from Osh would fair better?

@petermccloud

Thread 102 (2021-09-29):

Hall-Effect Tachometer

GeorgesOatesLarsen, 2021-09-29:
Should get these thoughts written down as an issue,

Here are the two candidates I am looking at, as far as tachs are concerned:

Good, but it is latch:
https://www.digikey.com/en/products/detail/texas-instruments/DRV5011ADLPG/11625531

Good alternative:
https://www.digikey.com/en/products/detail/diodes-incorporated/AH3365Q-P-B/6575183

Around 5mA draw, excluding power drawn by readout supply, but that should be tiny since the ESP32 is CMOS.

GeorgesOatesLarsen, 2021-09-29:
Through-hole hall-effect sensors, since they have a sensitivity axis conveniently perpendicular to the board plane!

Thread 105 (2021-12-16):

DUT13 Test Log

GeorgesOatesLarsen, 2021-12-16:
DUT13 Testing Log
Serial programming did NOT work at first, but magically fixed itself, suspect windows
Hall effect sensor worked at first, but was left running for 24 hours, and became latched high.
No hypothesis for cause, after removing unnecessary 100k resitor which should not have caused any problems, hall effect sensor began working again. Suspect what actually fixed it was sustained power-off state, rather than removal of resistor. Not sure. Will run 24 hours again to see if it happens again.

On battery power, system draws 0.01A to 0.02A, within spec. SYSPOW shows 7.2V, 0V alternation as expected.
On Engine power, system draws 0.08A, within spec. SYSPOW shows 8.4V to 0V

I do not have the ability to test power swap between battery and engine power; Need fresh batteries for that test. All systems I have the ability to test are functioning as expected.

UPDATE:
Figured out the issue with the hall effect sensor. Cold solder joint. Could literally change the value on it by wiggling the sensor. Cleaned up the joints, wiggling no longer impacts sensor performance.

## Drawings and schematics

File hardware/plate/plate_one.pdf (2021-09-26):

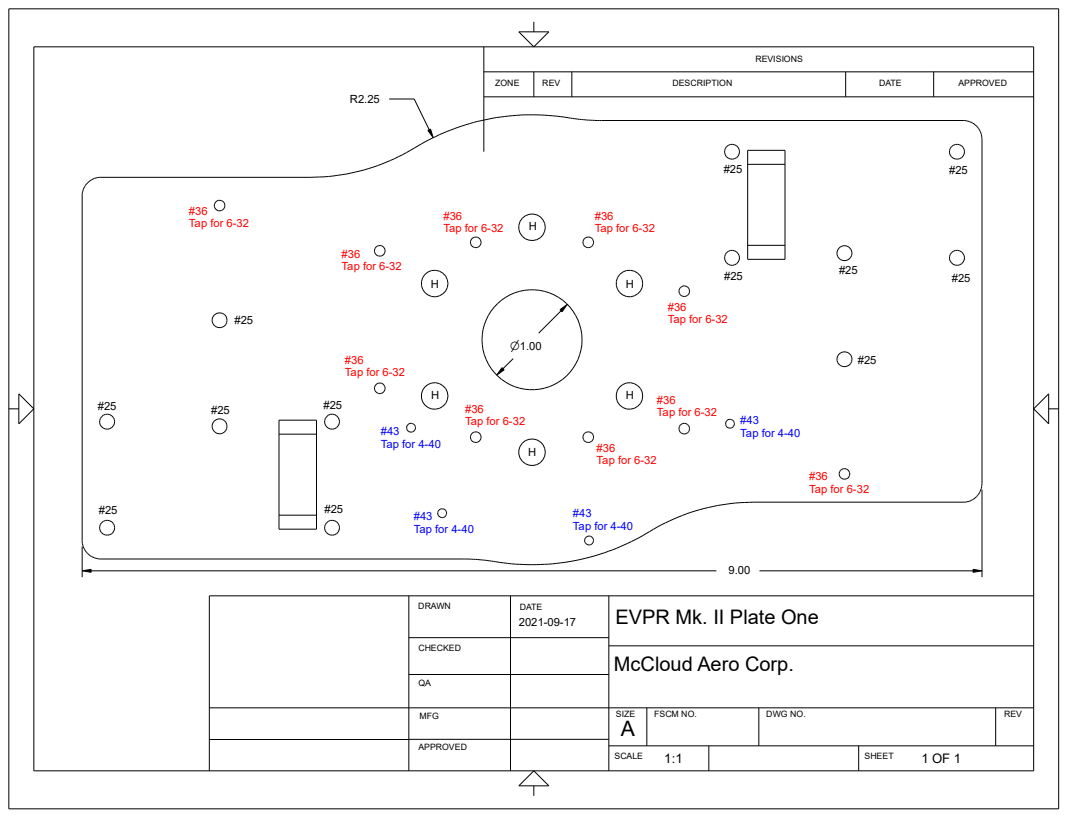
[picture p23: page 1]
#43 Tap for 4-40; #36 Tap for 6-32

REVISIONS

ZONE | REV | DESCRIPTION | DATE | APPROVED

DRAWN | DATE 2021-09-17 | EVPR Mk. II Plate One

CHECKED

McCloud Aero Corp.

MFG | | SIZE A | FSCM NO. | DWG NO. | REV

APPROVED

SCALE 1:1 | SHEET 1 OF 1

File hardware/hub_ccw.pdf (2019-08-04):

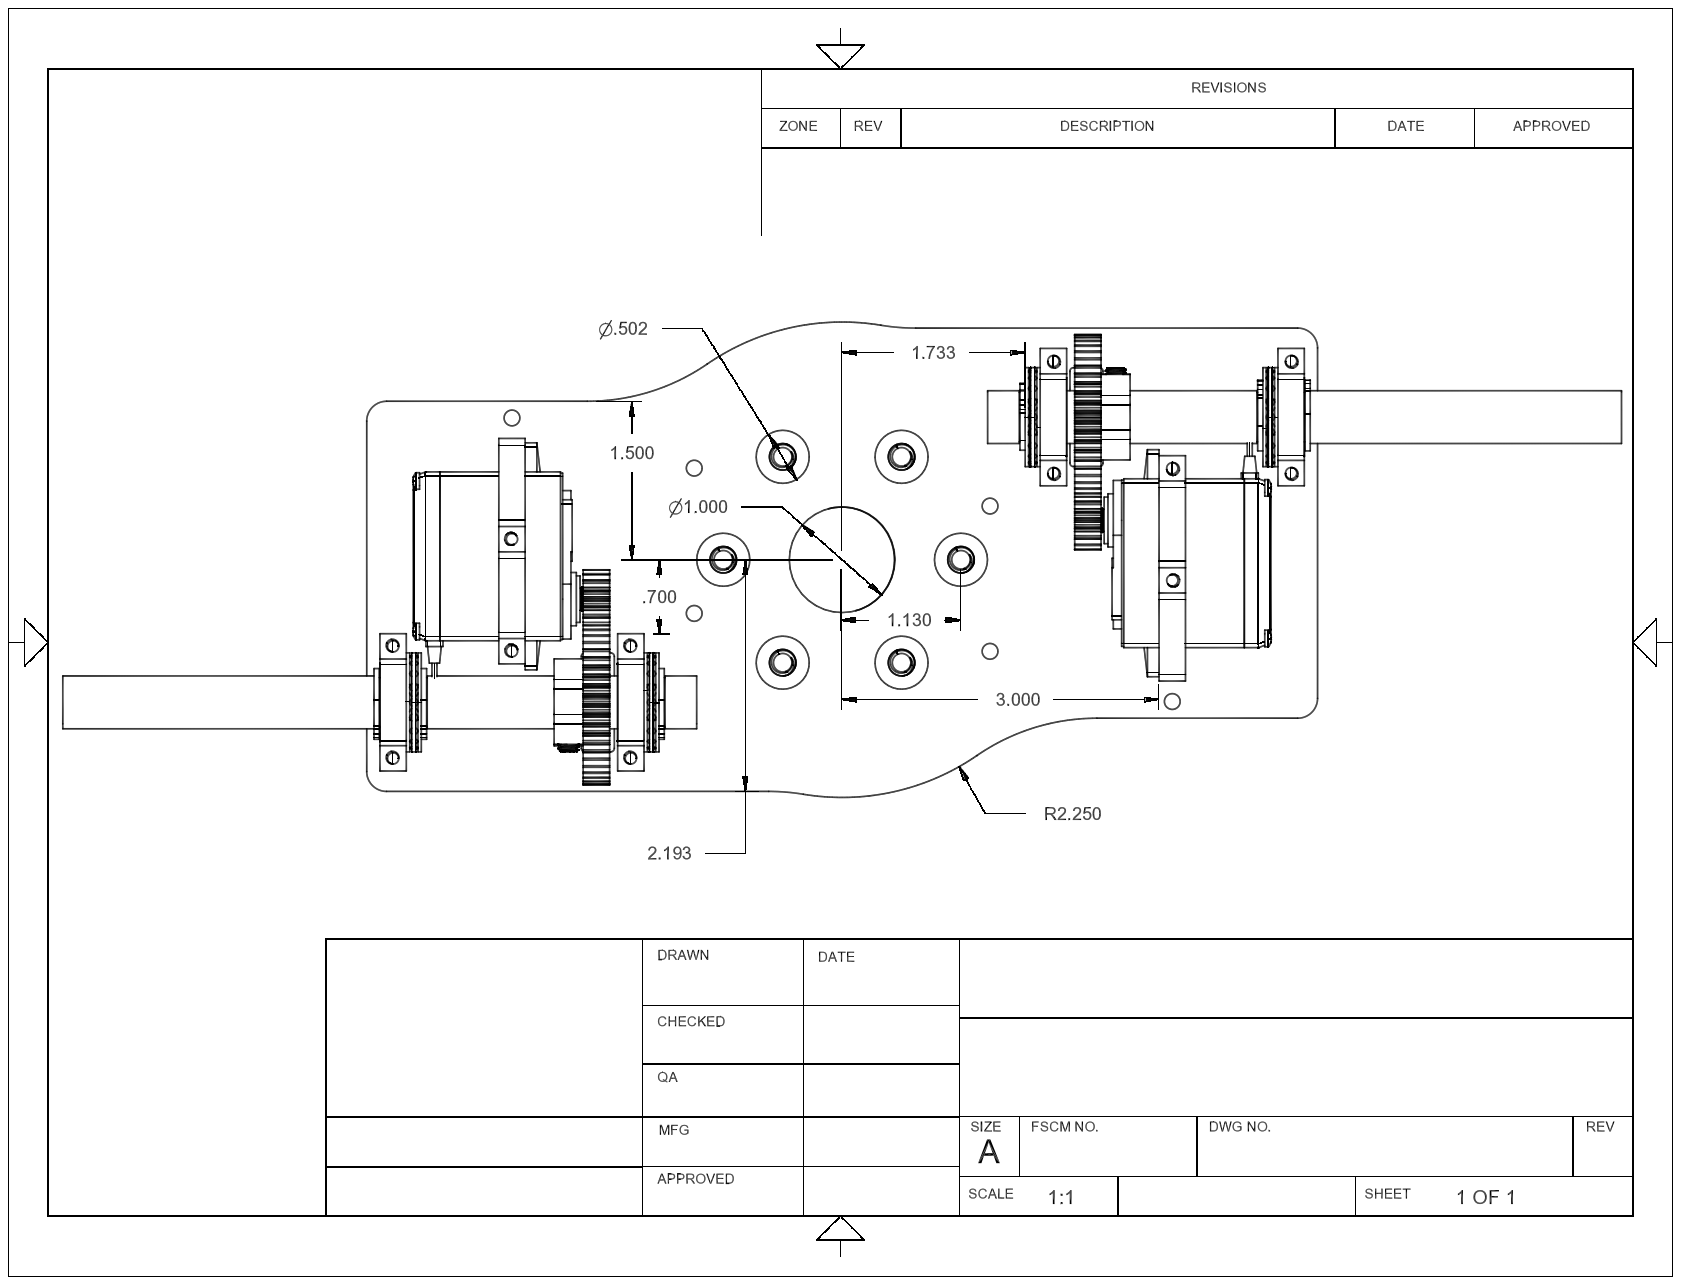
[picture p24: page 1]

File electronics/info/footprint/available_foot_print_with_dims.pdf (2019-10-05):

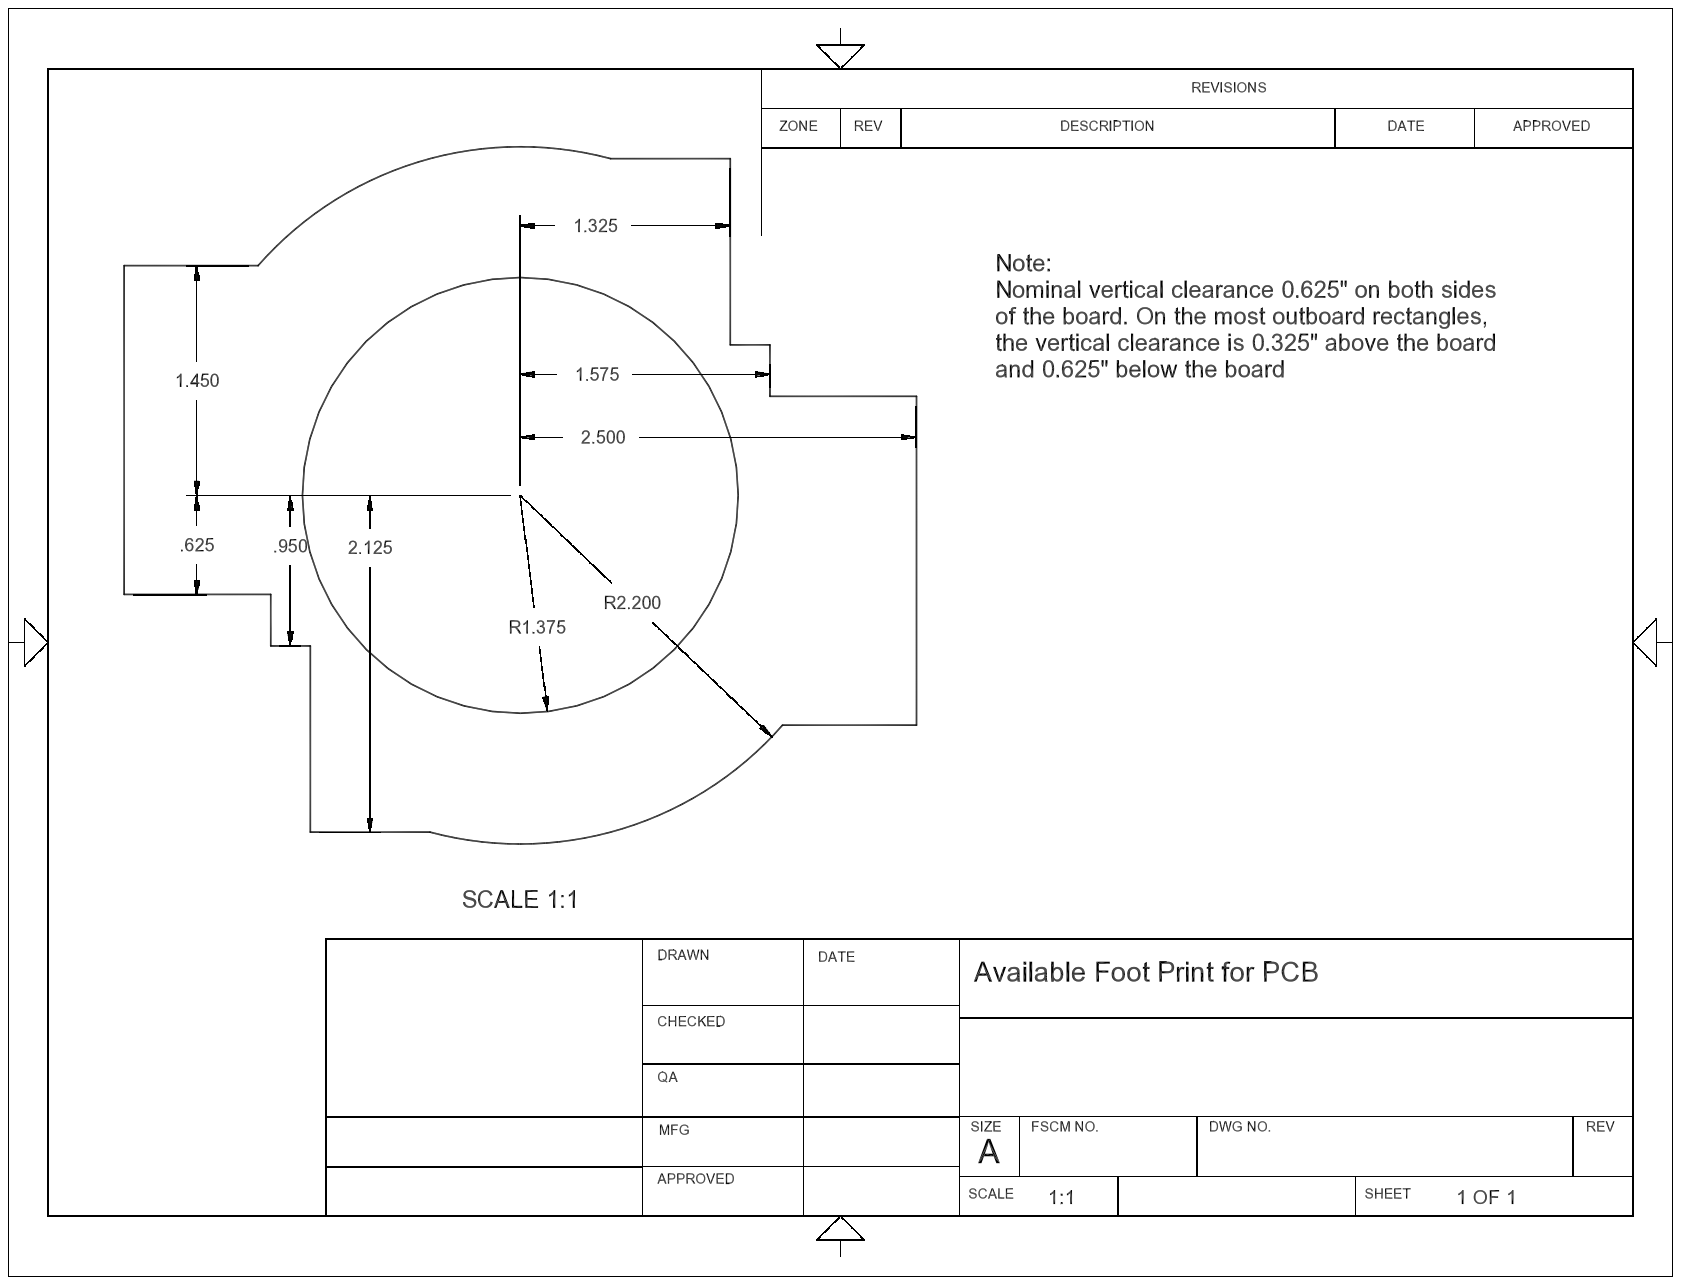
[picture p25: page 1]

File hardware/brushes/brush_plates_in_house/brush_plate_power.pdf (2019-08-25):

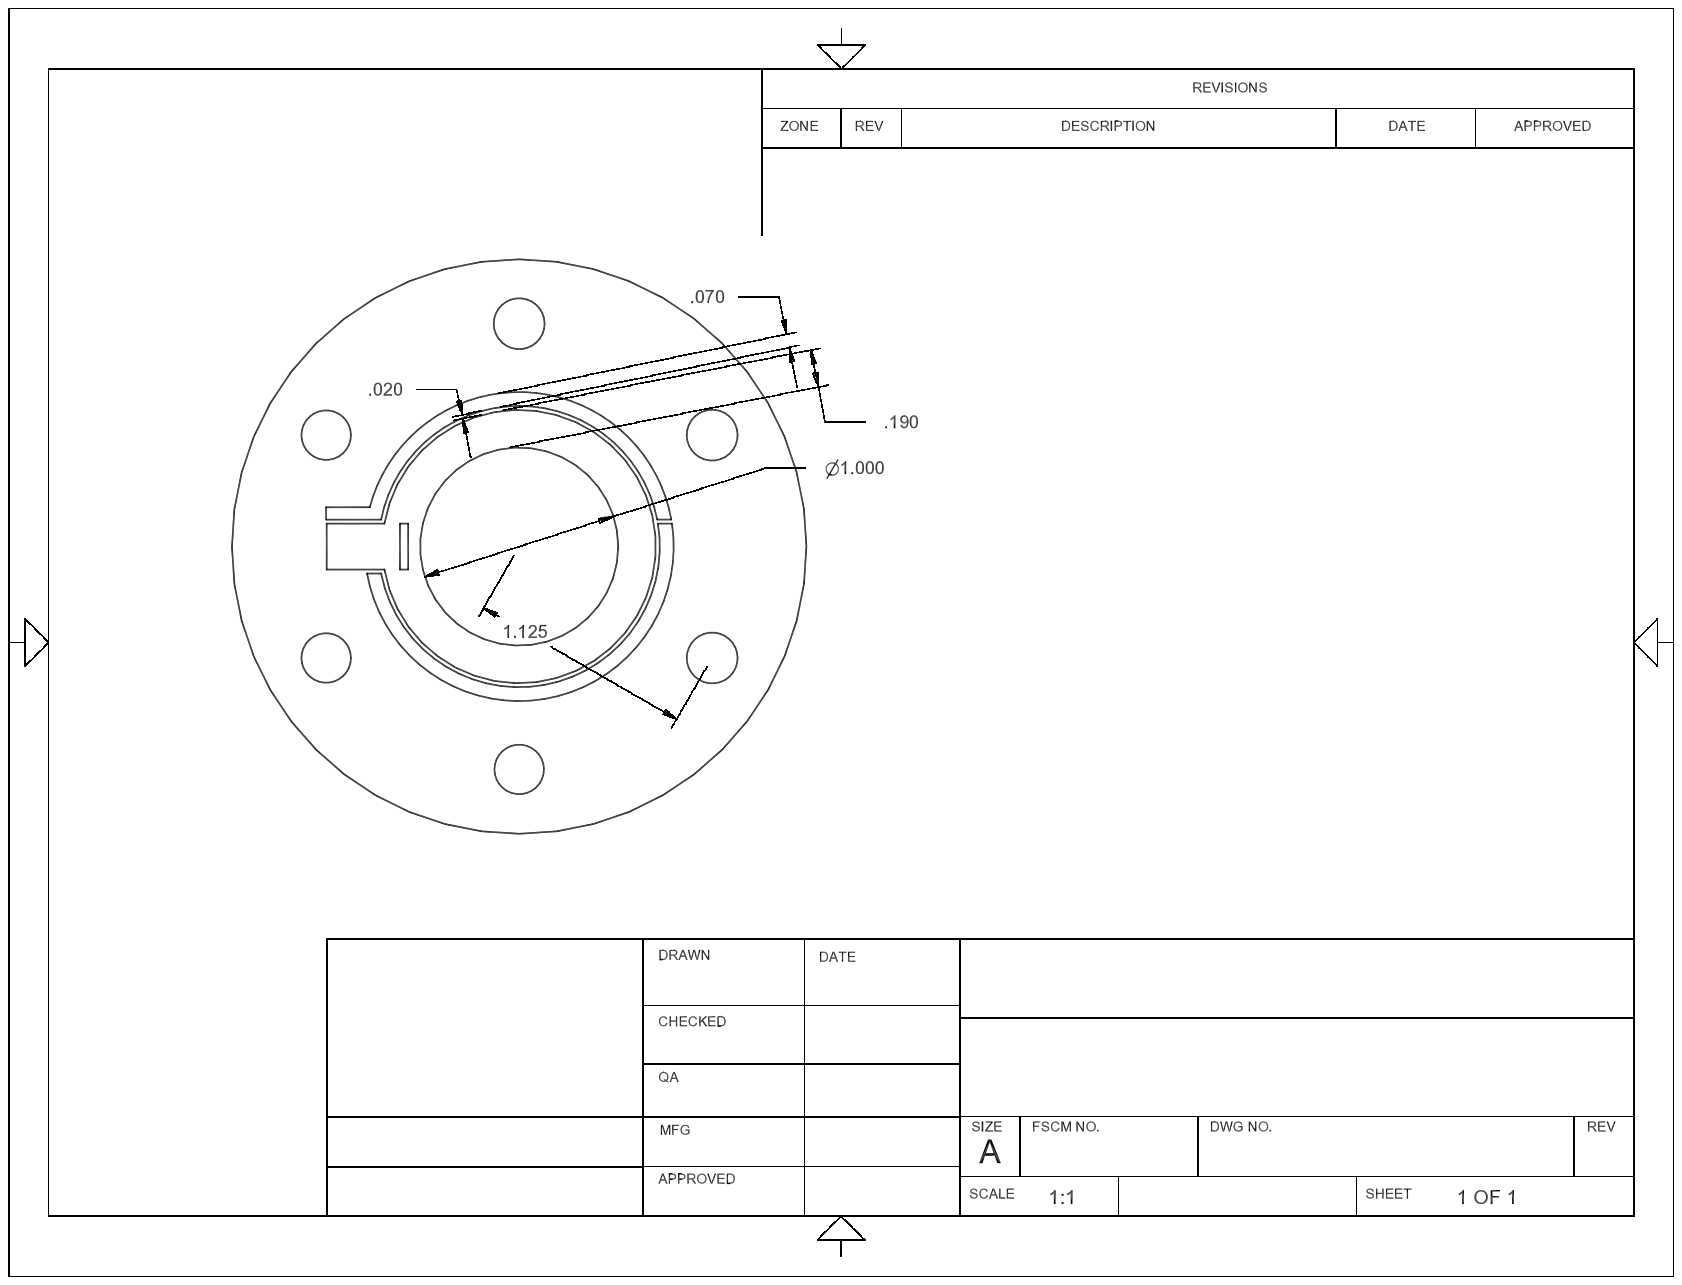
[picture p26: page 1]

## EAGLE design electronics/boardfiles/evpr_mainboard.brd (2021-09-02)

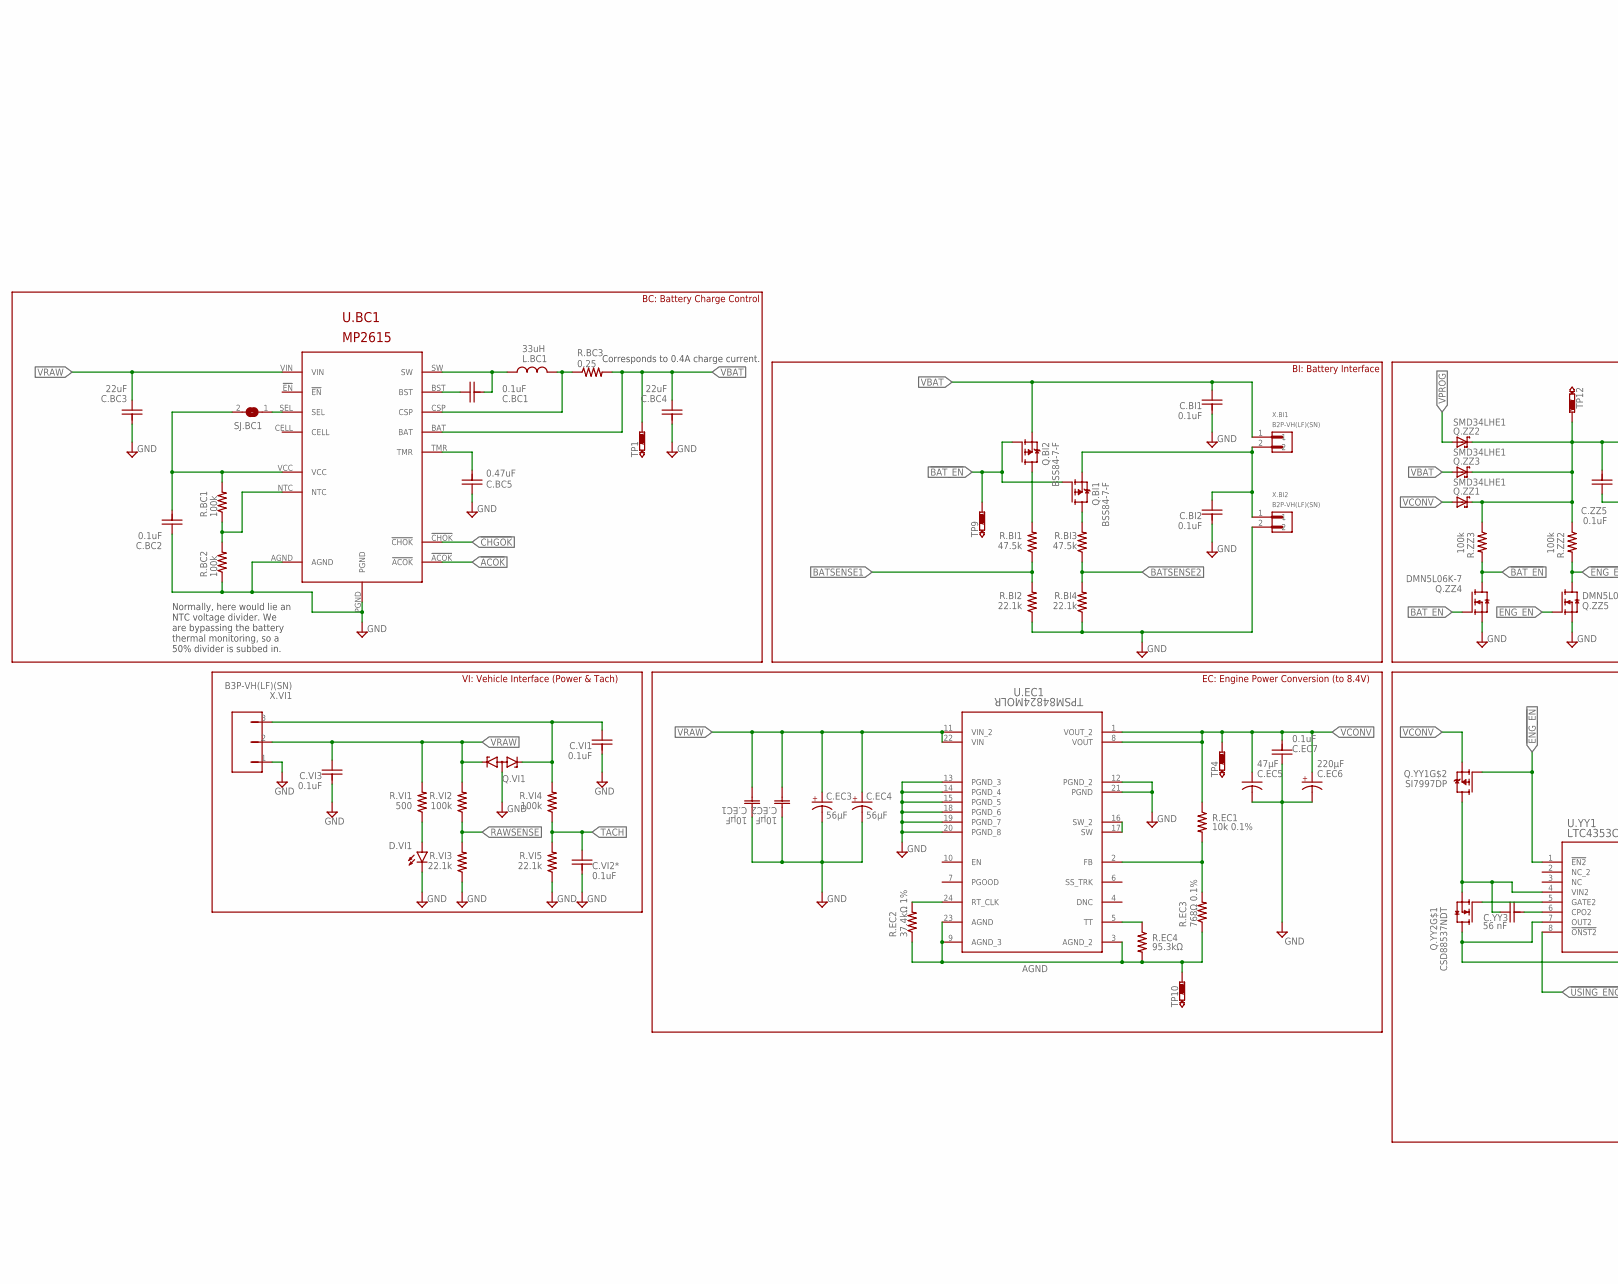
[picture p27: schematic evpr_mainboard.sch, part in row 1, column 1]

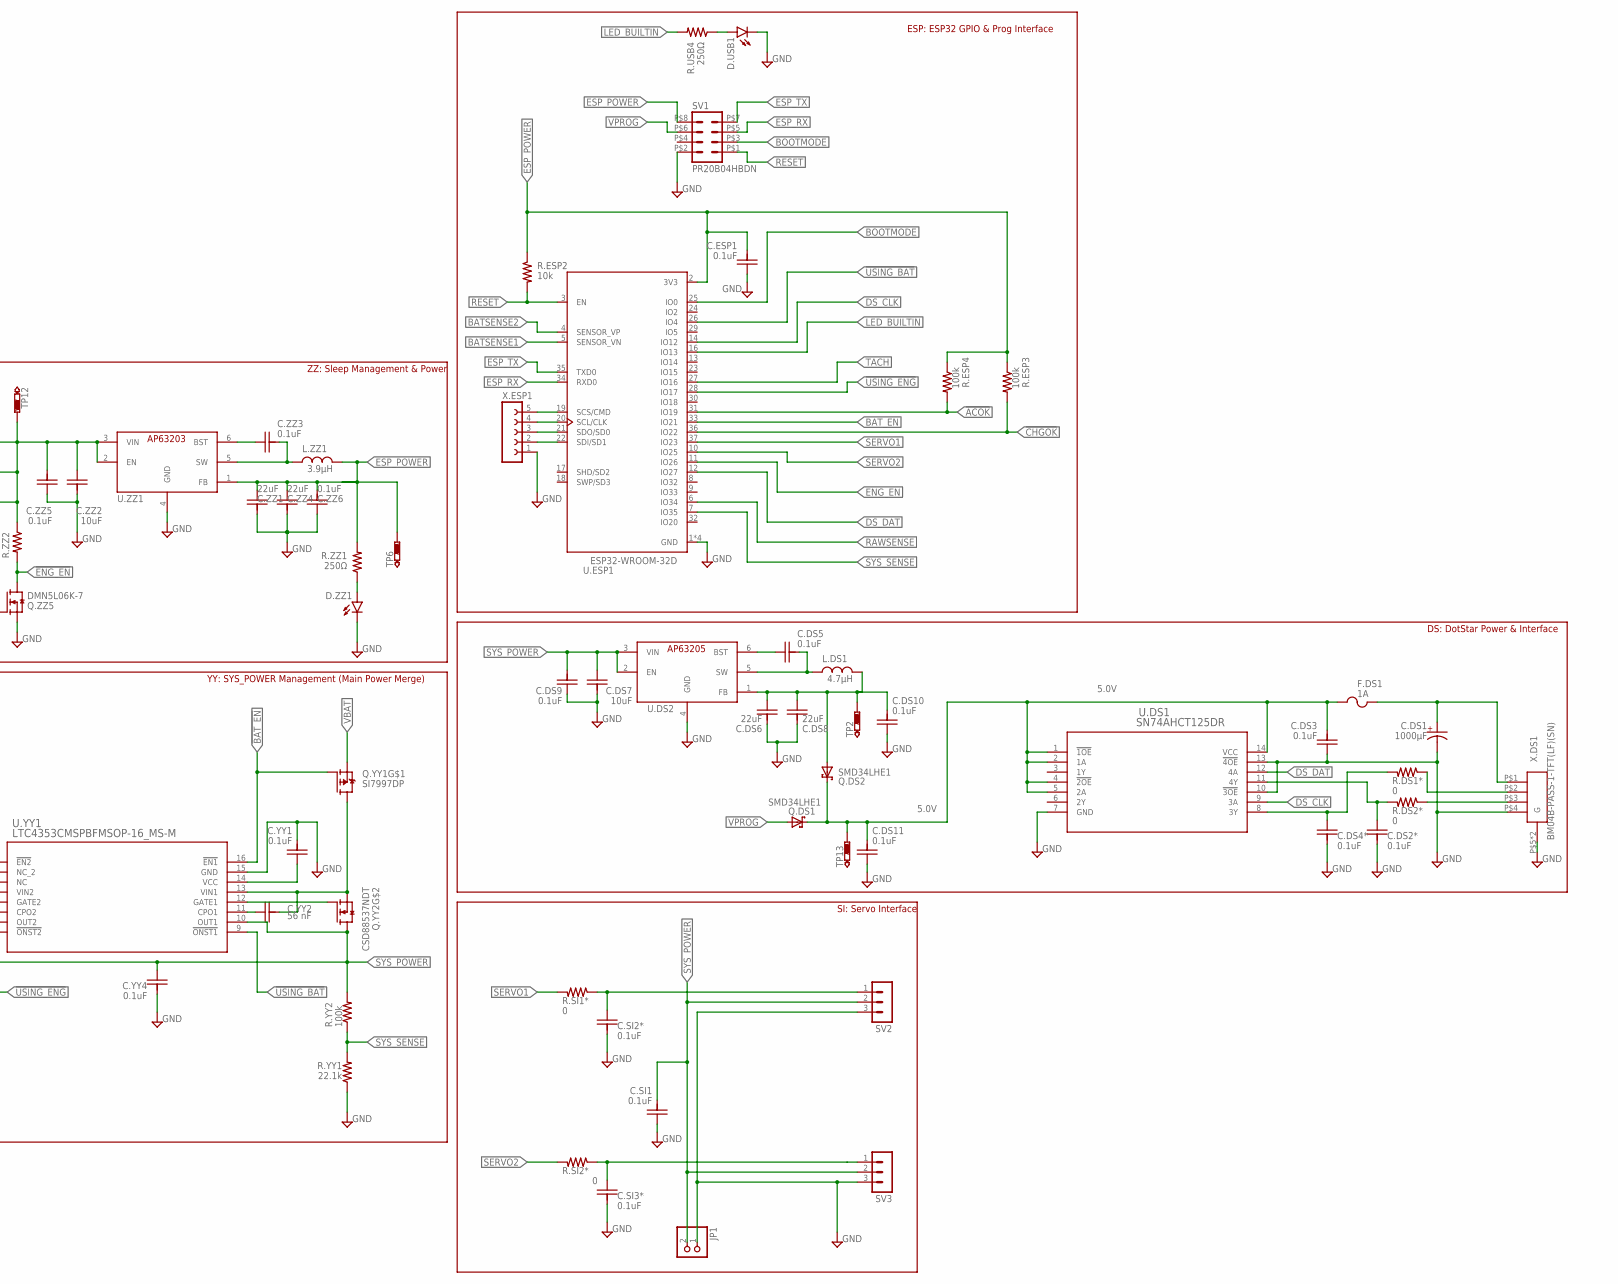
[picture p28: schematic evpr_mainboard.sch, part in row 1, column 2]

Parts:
C.BC1, C.BC2, C.BI1, C.BI2, C.DS2*, C.DS3, C.DS4*, C.DS5, C.DS9, C.DS10, C.DS11, C.EC7, C.ESP1, C.SI1, C.SI2*, C.SI3*, C.VI1, C.VI2*, C.VI3, C.YY1, C.YY4, C.ZZ3, C.ZZ5, C.ZZ6: 0.1uF; C0603
C.BC3, C.BC4, C.DS6, C.DS8, C.ZZ1, C.ZZ4: 22uF; C0603
C.BC5: 0.47uF; C0603
C.DS1: 1000µF; 810RADCAN
C.DS7, C.ZZ2: 10uF; C0603
C.EC1, C.EC2: 10µF; CAP_3225
C.EC3, C.EC4: 56µF; OSCON_SVPF_6.3MM
C.EC5: 47µF; C1210
C.EC6: 220µF; C6CYLCAP
C.YY2, C.YY3: 56 nF; C0603
D.USB1, D.VI1, D.ZZ1: LEDCHIP-LED0805; CHIP-LED0805
F.DS1: 1A; C1-M
JP1: PINHD-1X2; 1X02
L.BC1: 33uH; SRN5040TA
L.DS1: 4.7µH; SRR4818A-XXXX
L.ZZ1: 3.9µH; SRR4818A-XXXX
Q.BI1, Q.BI2: BSS84-7-F; SOT23
Q.DS1, Q.DS2, Q.ZZ1, Q.ZZ2, Q.ZZ3: SMD34LHE1; SOD-123HE1
Q.VI1: VESD16A2-03G-G3-08; SOT23
Q.YY1: SI7997DP; POWERPAK_SO8DUAL
Q.YY2: CSD88537NDT; SOIC8
Q.ZZ4, Q.ZZ5: DMN5L06K-7; SOT23
R.BC1, R.BC2, R.ESP3, R.ESP4, R.VI2, R.VI4, R.YY2, R.ZZ2, R.ZZ3: 100k; R0603
R.BC3: 0.25; R0603
R.BI1, R.BI3: 47.5k; R0603
R.BI2, R.BI4, R.VI3, R.VI5, R.YY1: 22.1k; R0603
R.DS1*, R.DS2*, R.SI1*, R.SI2*: 0; R0603
R.EC1: 10k 0.1%; R0603
R.EC2: 37.4kΩ 1%; R0603
R.EC3: 768Ω 0.1%; R0603
R.EC4: 95.3kΩ; R0603
R.ESP2: 10k; R0603
R.USB4, R.ZZ1: 250Ω; R0603
R.VI1: 500; R0603
SJ.BC1: SJ
SV1: PR20B04HBDN
SV2, SV3: MA03-1
TP1, TP2, TP4, TP6, TP9, TP10, TP12, TP13: PTR1TP10R; TP10R
U.BC1: MP2615; QFN16
U.DS1: SN74AHCT125DR; D14
U.DS2: AP63205; TSOT23-6
U.EC1: TPSM84824MOLR; MOL0024A
U.ESP1: ESP32-WROOM-32D; MODULE_ESP32-WROOM-32D
U.YY1: LTC4353CMSPBFMSOP-16_MS-M; MSOP-16_MS-M
U.ZZ1: AP63203; TSOT23-6
X.BI1, X.BI2: B2P-VH(LF)(SN)
X.DS1: BM04B-PASS-1-TFT(LF)(SN)
X.ESP1: FE05-1
X.VI1: B3P-VH(LF)(SN)

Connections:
5.0V: C.DS3.2, C.DS11.2, F.DS1.1, Q.DS1.C, Q.DS2.C, TP13.TP, U.DS1.1 (!1OE), U.DS1.2 (1A), U.DS1.4 (!2OE), U.DS1.5 (2A), U.DS1.14 (VCC)
!ACOK: R.ESP4.2, U.BC1.!ACOK, U.ESP1.31 (IO19)
!BAT_EN: Q.BI1.1 (G), Q.BI2.1 (G), Q.YY1.P$2 (G), Q.ZZ4.3 (D), R.ZZ3.2, TP9.TP, U.YY1.16 (!EN1)
!CHGOK: R.ESP3.2, U.BC1.!CHOK, U.ESP1.36 (IO22)
!ENG_EN: Q.YY1.P$4 (G), Q.ZZ5.3 (D), R.ZZ2.2, U.YY1.1 (!EN2)
!USING_BAT: U.ESP1.26 (IO4), U.YY1.9 (!ONST1)
!USING_ENG: U.ESP1.28 (IO17), U.YY1.8 (!ONST2)
AGND: R.EC2.1, R.EC3.1, R.EC4.2, TP10.TP, U.EC1.3 (AGND_2), U.EC1.9 (AGND_3), U.EC1.23 (AGND)
BATSENSE1: R.BI1.1, R.BI2.2, U.ESP1.5 (SENSOR_VN)
BATSENSE2: R.BI3.1, R.BI4.2, U.ESP1.4 (SENSOR_VP)
BAT_EN: Q.ZZ4.1 (G), U.ESP1.33 (IO21)
BOOTMODE: SV1.P$3 (3), U.ESP1.25 (IO0)
DS_CLK: U.DS1.9 (3A), U.ESP1.14 (IO12)
DS_DAT: U.DS1.12 (4A), U.ESP1.12 (IO27)
ENG_EN: Q.ZZ5.1 (G), U.ESP1.11 (IO26)
ESP_POWER: C.ESP1.2, C.ZZ1.1, C.ZZ4.1, C.ZZ6.2, L.ZZ1.P$2 (2), R.ESP2.1, R.ESP3.1, R.ESP4.1, R.ZZ1.2, SV1.P$8 (8), TP6.TP, U.ESP1.2 (3V3), U.ZZ1.1 (FB)
ESP_RX: SV1.P$5 (5), U.ESP1.34 (RXD0)
ESP_TX: SV1.P$7 (7), U.ESP1.35 (TXD0)
GND: C.BC2.1, C.BC3.2, C.BC4.2, C.BC5.1, C.BI1.2, C.BI2.2, C.DS1.C$2 (-), C.DS2*.2, C.DS3.1, C.DS4*.2, C.DS6.2, C.DS7.2, C.DS8.2, C.DS9.1, C.DS10.1, C.DS11.1, C.EC1.1, C.EC2.1, C.EC3.-, C.EC4.-, C.EC5.2, C.EC6.P$1 (-), C.EC7.1, C.ESP1.1, C.SI1.1, C.SI2*.2, C.SI3*.2, C.VI1.2, C.VI2*.2, C.VI3.2, C.YY1.2, C.YY4.2, C.ZZ1.2, C.ZZ2.2, C.ZZ4.2, C.ZZ5.1, C.ZZ6.1, D.USB1.C, D.VI1.C, D.ZZ1.C, JP1.1, Q.VI1.3 (AA), Q.ZZ4.2 (S), Q.ZZ5.2 (S), R.BC2.1, R.BI2.1, R.BI4.1, R.VI3.1, R.VI5.1, R.YY1.1, SV1.P$2 (2), SV2.3, SV3.3, U.BC1.AGND, U.BC1.PGND, U.DS1.7 (GND), U.DS1.10 (!3OE), U.DS1.13 (!4OE), U.DS2.4 (GND), U.EC1.12 (PGND_2), U.EC1.13 (PGND_3), U.EC1.14 (PGND_4), U.EC1.15 (PGND_5), U.EC1.18 (PGND_6), U.EC1.19 (PGND_7), U.EC1.20 (PGND_8), U.EC1.21 (PGND), U.ESP1.1 (GND), U.ESP1.15 (GND), U.ESP1.38 (GND), U.ESP1.39 (GND), U.YY1.15 (GND), U.ZZ1.4 (GND), X.BI2.2, X.DS1.P$4 (4), X.DS1.P$5 (G), X.DS1.P$6 (G), X.ESP1.1, X.VI1.1
LED_BUILTIN: R.USB4.2, U.ESP1.16 (IO13)
unnamed: R.EC1.2, R.EC3.2, U.EC1.2 (FB)
unnamed: Q.YY2.4 (G), U.YY1.12 (GATE1)
unnamed: C.YY3.1, Q.YY1.D$2A (D), Q.YY2.1 (S), U.YY1.4 (VIN2)
unnamed: C.YY2.2, Q.YY1.D$1B (D), Q.YY2.3 (S), U.YY1.13 (VIN1)
unnamed: C.BC5.2, U.BC1.TMR
unnamed: C.BI2.1, Q.BI1.2 (S), X.BI1.2, X.BI2.1
unnamed: C.ZZ2.1, C.ZZ5.2, Q.ZZ1.C, Q.ZZ2.C, Q.ZZ3.C, R.ZZ2.1, R.ZZ3.1, TP12.TP, U.ZZ1.2 (EN), U.ZZ1.3 (VIN)
unnamed: Q.YY2.2 (G), U.YY1.5 (GATE2)
unnamed: C.SI2*.1, R.SI1*.1, SV2.1
unnamed: C.SI3*.1, R.SI2*.1, SV3.1
unnamed: Q.BI2.3 (D), R.BI1.2
unnamed: C.ZZ3.1, U.ZZ1.6 (BST)
unnamed: U.EC1.16 (SW_2), U.EC1.17 (SW)
unnamed: R.EC2.2, U.EC1.24 (RT_CLK)
unnamed: C.DS2*.1, R.DS2*.2, U.DS1.11 (4Y)
unnamed: D.VI1.A, R.VI1.1
unnamed: D.USB1.A, R.USB4.1
unnamed: C.ZZ3.2, L.ZZ1.P$1 (1), U.ZZ1.5 (SW)
unnamed: C.DS4*.1, R.DS1*.2, U.DS1.8 (3Y)
unnamed: C.DS1.A$1 (+), F.DS1.2, X.DS1.P$1 (1)
unnamed: C.DS5.1, U.DS2.6 (BST)
unnamed: R.DS1*.1, X.DS1.P$2 (2)
unnamed: R.EC4.1, U.EC1.5 (TT)
unnamed: C.YY1.1, U.YY1.14 (VCC)
unnamed: Q.BI1.3 (D), R.BI3.2
unnamed: D.ZZ1.A, R.ZZ1.1
unnamed: C.YY2.1, U.YY1.11 (CPO1)
unnamed: C.YY3.2, U.YY1.6 (CPO2)
unnamed: R.DS2*.1, X.DS1.P$3 (3)
unnamed: R.BC1.1, R.BC2.2, U.BC1.NTC
unnamed: U.ESP1.19 (SCS/CMD), X.ESP1.5
unnamed: C.DS5.2, L.DS1.P$1 (1), U.DS2.5 (SW)
unnamed: C.DS6.1, C.DS8.1, C.DS10.2, L.DS1.P$2 (2), Q.DS2.A, TP2.TP, U.DS2.1 (FB)
unnamed: C.BC2.2, R.BC1.2, SJ.BC1.2, U.BC1.VCC
unnamed: L.BC1.P$2 (2), R.BC3.1, U.BC1.CSP
unnamed: SJ.BC1.1, U.BC1.SEL
unnamed: C.BC1.1, U.BC1.BST
unnamed: C.BC1.2, L.BC1.P$1 (1), U.BC1.SW
unnamed: U.ESP1.20 (SCL/CLK), X.ESP1.4
unnamed: U.ESP1.21 (SDO/SD0), X.ESP1.3
unnamed: U.ESP1.22 (SDI/SD1), X.ESP1.2
RAWSENSE: R.VI2.1, R.VI3.2, U.ESP1.6 (IO34)
RESET: R.ESP2.2, SV1.P$1 (1), U.ESP1.3 (EN)
SERVO1: R.SI1*.2, U.ESP1.37 (IO23)
SERVO2: R.SI2*.2, U.ESP1.10 (IO25)
SYS_POWER: C.DS7.1, C.DS9.2, C.SI1.2, C.YY4.1, JP1.2, Q.YY2.5 (D), Q.YY2.6 (D), Q.YY2.7 (D), Q.YY2.8 (D), R.YY2.2, SV2.2, SV3.2, U.DS2.2 (EN), U.DS2.3 (VIN), U.YY1.7 (OUT2), U.YY1.10 (OUT1)
SYS_SENSE: R.YY1.2, R.YY2.1, U.ESP1.7 (IO35)
TACH: C.VI2*.1, R.VI4.1, R.VI5.2, U.ESP1.27 (IO16)
TACH_RAW: C.VI1.1, Q.VI1.2 (K1), R.VI4.2, X.VI1.3
VBAT: C.BC4.1, C.BI1.1, Q.BI2.2 (S), Q.YY1.P$1 (S), Q.ZZ3.A, R.BC3.2, TP1.TP, U.BC1.BAT, X.BI1.1
VCONV: C.EC5.1, C.EC6.P$2 (+), C.EC7.2, Q.YY1.P$3 (S), Q.ZZ1.A, R.EC1.1, TP4.TP, U.EC1.1 (VOUT_2), U.EC1.8 (VOUT)
VPROG: Q.DS1.A, Q.ZZ2.A, SV1.P$6 (6)
VRAW: C.BC3.1, C.EC1.2, C.EC2.2, C.EC3.+, C.EC4.+, C.VI3.1, Q.VI1.1 (K2), R.VI1.2, R.VI2.2, U.BC1.VIN, U.EC1.11 (VIN_2), U.EC1.22 (VIN), X.VI1.2

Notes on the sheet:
VI: Vehicle Interface (Power & Tach)
EC: Engine Power Conversion (to 8.4V)
BC: Battery Charge Control
BI: Battery Interface
YY: SYS_POWER Management (Main Power Merge)
DS: DotStar Power & Interface
SI: Servo Interface
ESP: ESP32 GPIO & Prog Interface
ZZ: Sleep Management & Power
Normally, here would lie an NTC voltage divider. We are bypassing the battery thermal monitoring, so a 50% divider is subbed in.
Corresponds to 0.4A charge current.

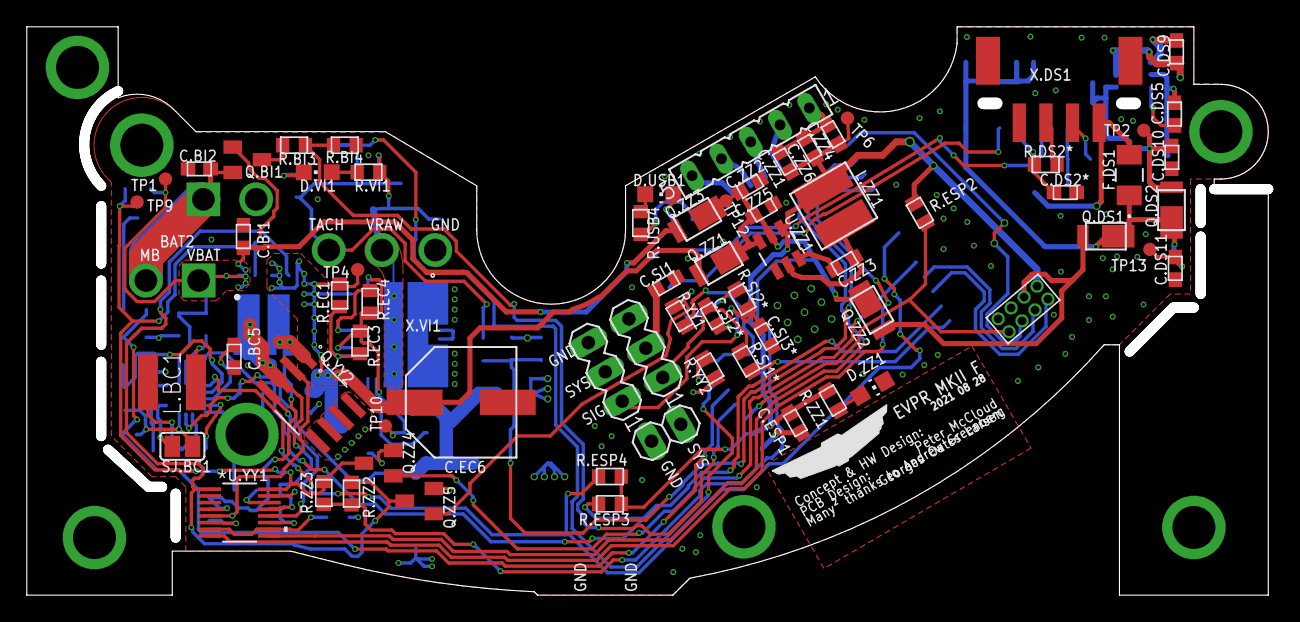
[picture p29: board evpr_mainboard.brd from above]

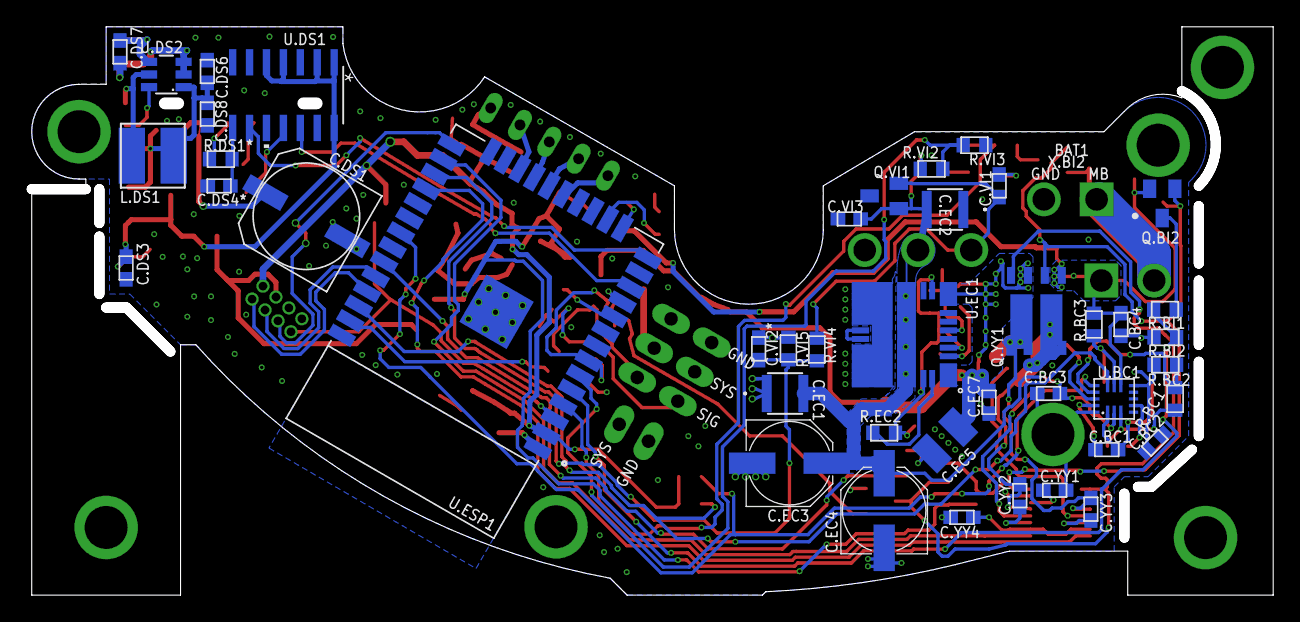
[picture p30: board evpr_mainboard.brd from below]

Board: 4 copper layers, 93.2 x 42.7 mm, 115 parts (44 on the bottom side), 73 nets.

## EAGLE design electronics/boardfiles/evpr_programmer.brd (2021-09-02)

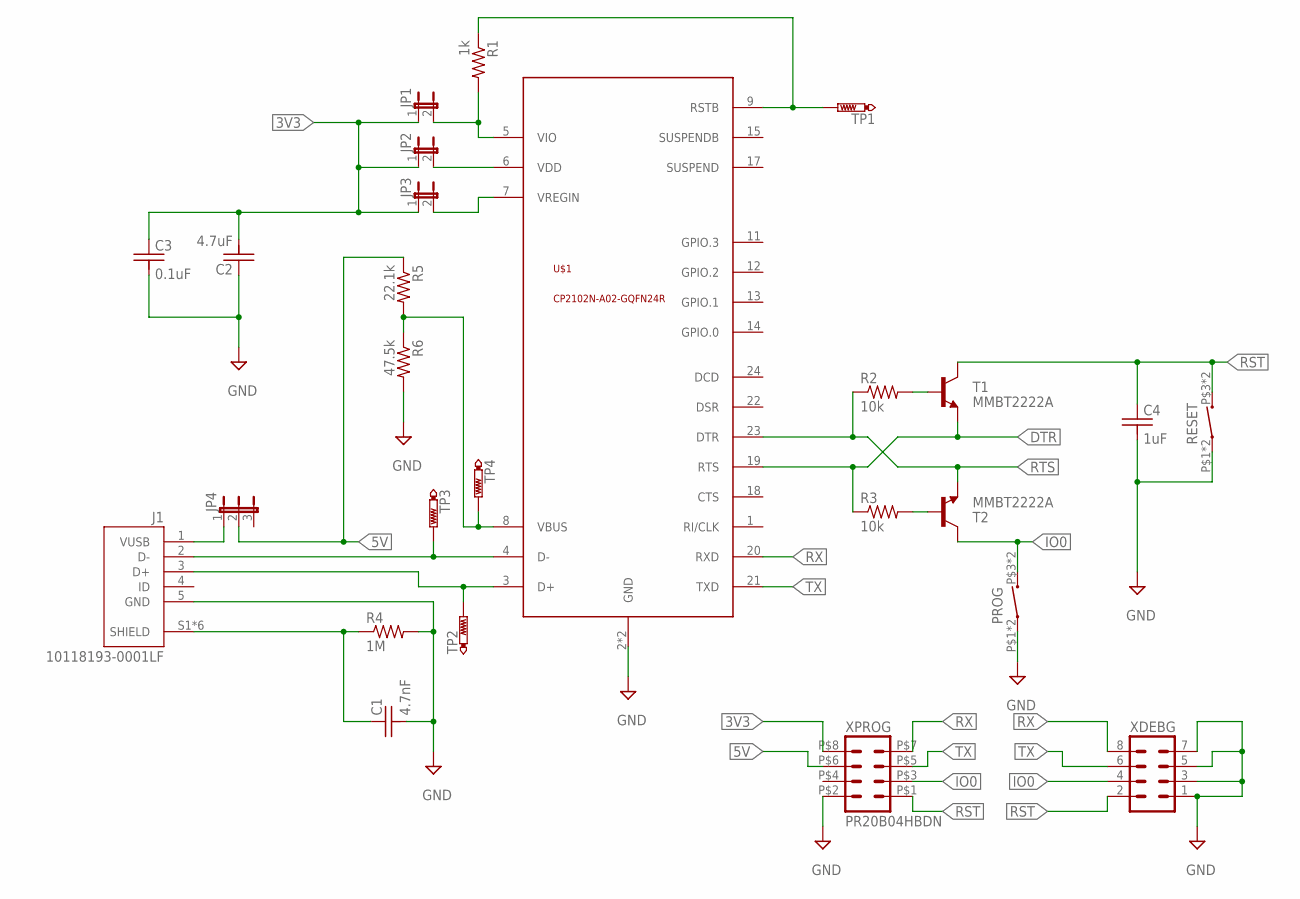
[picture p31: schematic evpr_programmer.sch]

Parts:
C1: 4.7nF; C0603
C2: 4.7uF; C0603
C3: 0.1uF; C0603
C4: 1uF; C0603
J1: 10118193-0001LF; FCI_10118193-0001LF
JP1, JP2, JP3: JP1E; JP1
JP4: JP2E; JP2
PROG: MOMENTARY_SWITCH; PTS645
R1: 1k; R0603
R2, R3: 10k; R0603
R4: 1M; R0603
R5: 22.1k; R0603
R6: 47.5k; R0603
RESET: MOMENTARY_SWITCH; PTS645
T1, T2: MMBT2222A; SOT23-BEC
TP1, TP2, TP3, TP4: PTR1TP10R; TP10R
U$1: CP2102N-A02-GQFN24R; QFN24-4X4
XDEBG: MA04-2
XPROG: PR20B04HBDN

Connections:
3V3: C2.2, C3.1, JP1.1, JP2.1, JP3.1, XPROG.P$8 (8)
5V: JP4.2, R5.1, XPROG.P$6 (6)
DTR: R3.1, T1.E, U$1.19 (RTS)
GND: C1.2, C2.1, C3.2, C4.2, J1.5 (GND), PROG.P$1 (1), PROG.P$2 (1), R4.2, R6.2, RESET.P$1 (1), RESET.P$2 (1), U$1.2 (GND), U$1.EXP (GND), XDEBG.1, XDEBG.3, XDEBG.5, XDEBG.7, XPROG.P$2 (2)
IO0: PROG.P$3 (2), PROG.P$4 (2), T2.C, XDEBG.4, XPROG.P$3 (3)
unnamed: J1.1 (VUSB), JP4.1
unnamed: JP2.2, U$1.6 (VDD)
unnamed: R1.1, TP1.TP, U$1.9 (RSTB)
unnamed: JP1.2, R1.2, U$1.5 (VIO)
unnamed: C1.1, J1.S1 (SHIELD), J1.S2 (SHIELD), J1.S3 (SHIELD), J1.S4 (SHIELD), J1.S5 (SHIELD), J1.S6 (SHIELD), R4.1
unnamed: R3.2, T2.B
unnamed: R2.2, T1.B
unnamed: J1.3 (D+), TP2.TP, U$1.3 (D+)
unnamed: J1.2 (D-), TP3.TP, U$1.4 (D-)
unnamed: JP3.2, U$1.7 (VREGIN)
unnamed: R5.2, R6.1, TP4.TP, U$1.8 (VBUS)
RST: C4.1, RESET.P$3 (2), RESET.P$4 (2), T1.C, XDEBG.2, XPROG.P$1 (1)
RTS: R2.1, T2.E, U$1.23 (DTR)
RX: U$1.20 (RXD), XDEBG.8, XPROG.P$7 (7)
TX: U$1.21 (TXD), XDEBG.6, XPROG.P$5 (5)

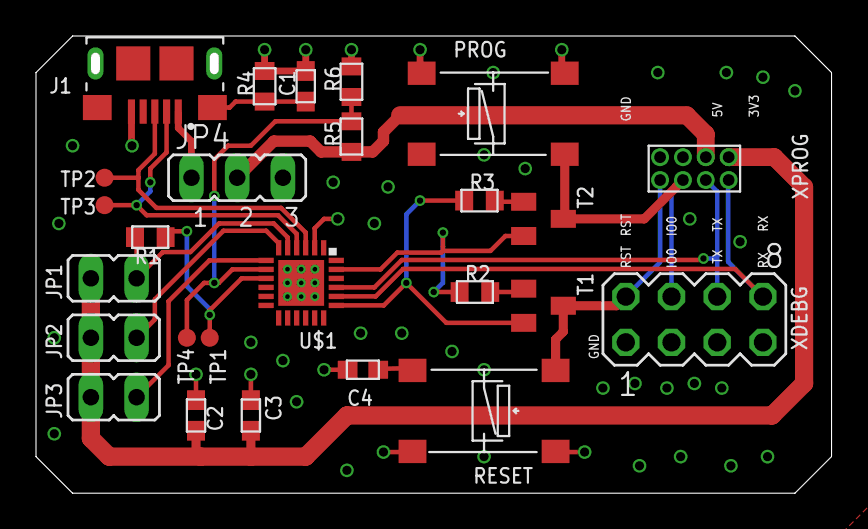
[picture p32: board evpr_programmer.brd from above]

Board: 2 copper layers, 44.2 x 25.4 mm, 26 parts (0 on the bottom side), 20 nets.

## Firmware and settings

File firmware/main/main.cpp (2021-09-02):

/*
 * This file serves to load in one of the primary modules: Head, Rotor, or Monitor
 * It also serves as a C entry point for C++ files, hence all the extern C nonsense.
 * Really, it's boilerplate you can ignore. Check the evprmonitor, evprhead, and evprrotor modules.
*/

#include "evprhead.h"
#include "evprrotor.h"
#include "evprmonitor.h"
#include "esp_log.h"

#ifdef __cplusplus
extern "C" {
#endif

#include "main.h"
void app_main()
{
    ESP_LOGI("MAIN", "The mode is %d", CONFIG_EVPR_NODETYPE);
    #if CONFIG_EVPR_NODETYPE==EVPR_HEAD
        ESP_LOGI("MAIN", "Booting as head.");
        EVPRH_main();
    #endif
    #if CONFIG_EVPR_NODETYPE==EVPR_ROTOR
        ESP_LOGI("MAIN", "Booting as rotor.");
        EVPRR_main();
    #endif
    #if CONFIG_EVPR_NODETYPE==EVPR_MONITOR
        ESP_LOGI("MAIN", "Booting as monitor.");
        //EVPRMonitor_main();
    #endif
}

#ifdef __cplusplus
}
#endif

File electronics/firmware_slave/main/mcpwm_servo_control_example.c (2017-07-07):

/* servo motor control example

   This example code is in the Public Domain (or CC0 licensed, at your option.)

   Unless required by applicable law or agreed to in writing, this
   software is distributed on an "AS IS" BASIS, WITHOUT WARRANTIES OR
   CONDITIONS OF ANY KIND, either express or implied.
*/
#include <stdio.h>

#include "freertos/FreeRTOS.h"
#include "freertos/task.h"
#include "esp_attr.h"

#include "driver/mcpwm.h"
#include "soc/mcpwm_reg.h"
#include "soc/mcpwm_struct.h"

//You can get these value from the datasheet of servo you use, in general pulse width varies between 1000 to 2000 mocrosecond
#define SERVO_MIN_PULSEWIDTH 1000 //Minimum pulse width in microsecond
#define SERVO_MAX_PULSEWIDTH 2000 //Maximum pulse width in microsecond
#define SERVO_MAX_DEGREE 90 //Maximum angle in degree upto which servo can rotate

static void mcpwm_example_gpio_initialize()
{
    printf("initializing mcpwm servo control gpio......\n");
    mcpwm_gpio_init(MCPWM_UNIT_0, MCPWM0A, 16);    //Set GPIO 16 as PWM0A, to which servo is connected
    mcpwm_gpio_init(MCPWM_UNIT_0, MCPWM0B, 17);    //Set GPIO 17 as PWM0B, to which servo is connected
}

/**
 * @brief Use this function to calcute pulse width for per degree rotation
 *
 * @param  degree_of_rotation the angle in degree to which servo has to rotate
 *
 * @return
 *     - calculated pulse width
 */
static uint32_t servo_per_degree_init(uint32_t degree_of_rotation)
{
    uint32_t cal_pulsewidth = 0;
    cal_pulsewidth = (SERVO_MIN_PULSEWIDTH + (((SERVO_MAX_PULSEWIDTH - SERVO_MIN_PULSEWIDTH) * (degree_of_rotation)) / (SERVO_MAX_DEGREE)));
    return cal_pulsewidth;
}

/**
 * @brief Configure MCPWM module
 */
void mcpwm_example_servo_control(void *arg)
{
    uint32_t angle, count;
    //1. mcpwm gpio initialization
    mcpwm_example_gpio_initialize();

    //2. initial mcpwm configuration
    printf("Configuring Initial Parameters of mcpwm......\n");
    mcpwm_config_t pwm_config;
    pwm_config.frequency = 50;    //frequency = 50Hz, i.e. for every servo motor time period should be 20ms
    pwm_config.cmpr_a = 0;    //duty cycle of PWMxA = 0
    pwm_config.cmpr_b = 0;    //duty cycle of PWMxb = 0
    pwm_config.counter_mode = MCPWM_UP_COUNTER;
    pwm_config.duty_mode = MCPWM_DUTY_MODE_0;
    mcpwm_init(MCPWM_UNIT_0, MCPWM_TIMER_0, &pwm_config);    //Configure PWM0A & PWM0B with above settings
    mcpwm_init(MCPWM_UNIT_0, MCPWM_TIMER_1, &pwm_config);    //Configure PWM0A & PWM0B with above settings
    while (1) {
        for (count = 0; count < SERVO_MAX_DEGREE; count++) {
            printf("Angle of rotation: %d\n", count);
            angle = servo_per_degree_init(count);
            printf("pulse width: %dus\n", angle);
            mcpwm_set_duty_in_us(MCPWM_UNIT_0, MCPWM_TIMER_0, MCPWM_OPR_A, angle);
            mcpwm_set_duty_in_us(MCPWM_UNIT_0, MCPWM_TIMER_0, MCPWM_OPR_B, angle);
            vTaskDelay(10);     //Add delay, since it takes time for servo to rotate, generally 100ms/60degree rotation at 5V
        }
    }
}

void app_main()
{
    printf("Testing servo motor.......\n");
    xTaskCreate(mcpwm_example_servo_control, "mcpwm_example_servo_control", 4096, NULL, 5, NULL);
}

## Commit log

2016-10-02 added variable pitch dir, moved prior designs to fixed pitch dir
    [63215K530_STAINLESS STEEL BALL JOINT SWIVEL BEARING.STEP, 8632T146_D-PROFILE SHAFT.STEP, 90128A132_ZNC-PLTD ALLOY STL SCKT HEAD CAP SCREW.STEP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]
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2017-04-13 CAD updates to resize plates, add bolts, servos
    [MG996R.SLDASM, servo.SLDPRT, shaft.SLDPRT]
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2017-04-13 fixed error with spacers
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2017-04-17 updates to rotor plates and created tool paths
    [plate.stl]
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2017-05-27 reworked CAD for gear design
    [575124.STEP, 615286.STEP]
2017-05-28 added toolpath for lower plate, created upper plate CAD
    [plate.stl, plate_lower.stl]
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2017-06-07 updates to spacer, reworked images
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2017-08-13 renamed plate_lower and plate_upper to plate_one and plate_two
    [plate_one.stl, plate_two.stl]
2017-08-13 updated tool paths for plates to reflect change in servo orientation
    [plate_one.stl, plate_two.stl]
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2017-09-16 seems to be reading from UART, but MAVLINK messages are not being read correctly
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2017-10-13 finished flipping second servo direction
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2017-10-13 fixed rotor blade in assembly model
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2017-10-27 Revert "added socket functions"
    This reverts commit f4d7e226c8c40dc4b52b1424190b2f64491436c5.
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2017-12-15 updated slave firmware to use correct status pin
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2018-01-19 merged uart.c into main.c to avoid issues with espnow_send
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2018-02-11 removed alternate design files, renamed design_A to hardware
    [575124.STEP, 615286.STEP, 63215K530_STAINLESS STEEL BALL JOINT SWIVEL BEARING.STEP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]
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2019-08-03 fixed dimensions for ground brush plate
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2019-08-06 changed bolt spacers to be 6061-T6 and reduced diameter
    [available_foot_print_in.dxf]
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2019-08-31 added battery assemblies to hub. interference present between gear and battery
2019-09-04 updated battey holder and modified plate two to fit the new holder
    [battery_holder_ccw.stl]
2019-09-05 fixed battery holder regression, updated plate 2 holes for tapping
    [battery_holder_ccw.stl]
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2019-09-14 changed battery holder to be single common config, add 3d printer files
    [battery_holder.curaproject.3mf, battery_holder.stl]
2019-09-18 updates to brush holder to allow clearance for electrical connections
    [brush_holder_mm.stl]
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2019-09-30 finalized brush holder design around helwig brush #393
    [brush_design.ods, brush_holder_mm.curaproject.3mf, brush_holder_mm.stl]
2019-10-05 cleaned up brushes, updated available foot print for PCB
    [available_foot_print_in.dxf]
2019-10-06 moved brush plate ground CAD, added files for cnc
    [brush_plate_ground_in.stl]
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2019-10-20 Flip polarity of PoR, remove shutdown main transistor, remove old ORing circuit, combined both into single unified power control circuit using ideal diode power ORing circuit.
    [evpr.brd, evpr.sch]
2019-10-30 Added power save and reset disable transistors. Added prototyping interconnects. Merged 3.3v, 5v, and USB blocks. Redid block arrangement.
    [evpr.brd, evpr.sch]
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2019-12-04 updates to servo sizing plots for 42in rotor
    [servo_sizing.ods]
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2019-12-17 Deep cleanup of schematic -- Values added, component sources transferred, labels aligned, etc
    [evpr.brd, evpr.sch]
2019-12-21 Fixed power save for battery sensing
    [evpr.brd, evpr.sch]
2019-12-22 routing and board fixes
    [evpr.brd, evpr.sch]
2019-12-28 Whew. Lots of routing. Lots of minor circuit changes. Routing is 99% done, just finishing touches are remaining.
    [evpr.brd, evpr.sch]
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2019-12-28 minor fixes to brush holder for labels and wire path
    [brush_holder_mm.curaproject.3mf, brush_holder_mm.stl]
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2019-12-29 Routing complete. All DRC/ERC checks except for USB port silliness performed and resolved. Test points added.
    [evpr.brd, evpr.sch]
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2020-01-11 Add oshparks file not contianing external screw reference
    [evpr_osh.brd, evpr_osh.sch]
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2020-01-18 further updates to D blade to get shrinkage adjustments correct
    [rotor_blade_42_dia_template_ccw_foam_core_plug.3mf, rotor_blade_ccw_42_dia_D_blade.3mf]
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2020-01-23 Updated all part numbers, created BOM, created order recommendation
    [EVPR BOM.ods, R&D Digikey Cart.csv, evpr.brd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]
2020-02-01 fixed battery mount holes on plate
2020-02-01 fixed tap holes for brushes
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2020-02-04 updated plate stl files, added units to filenames
    [plate_one.stl, plate_one_in.stl, plate_two.stl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]
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2020-02-23 fixed hub assembly
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2020-02-23 modified plate pockets to be deeper and wider
    [plate_one_in.stl, plate_two_in.stl]
2020-03-21 Update serial interface chip to only receive power from USB plug, utilize internal regulator instead of board 3.3V regulator. Also update bypass caps to be to spec. Also added .gitignore for electron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
    [evpr.brd, evpr.sch]
2020-03-21 Completely redid sub 8V power path to support ESP32 deep-sleep as primary powersave mechagnism.
    [EVPR BOM.ods, R&D Digikey Cart.csv, evpr.brd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]
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2020-03-22 Altered Battery Charge Symbol and cleaned up battery charge schematic
    [evpr.brd, evpr.sch]
2020-03-22 Replaced R31 and R2 with R8 and R32 respectively, 0603 outline and corrected part selection.
    [evpr.brd, evpr.sch]
2020-03-22 Replaced Dot-Star, Servo, PAD connectors with new JST-PA SMD connectors, saving significant board space.
    [evpr.brd, evpr.sch]
2020-03-22 Updated all DPAK components to use single package with detailed tkeepout
    [evpr.brd, evpr.sch]
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2020-03-22 Replace passives with 0603 wherever possible.
    [evpr.brd, evpr.sch]
2020-03-22 Added EMI Testing optionals
    [evpr.brd, evpr.sch]
2020-03-22 Added testpoints; Reviewed all testpoints; Corrected 3.3V converter to AP63203
    [evpr.brd, evpr.sch]
2020-03-23 Update all component names to follow new standard naming system
    [evpr.brd, evpr.sch]
2020-03-24 Hacked USB profile to have wires on internal layers. Seems to make Eagle behave.
    [evpr.brd, evpr.sch]
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2020-03-28 Minor odds and ends, BOM generation and processing.
    [bom.csv, evpr.brd, evpr.sch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]
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2020-08-06 Created first pass of rev 3, also created mini-boards for osh
    [evpr.brd, evpr.sch, evpr_mini.brd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]
2020-10-11 Applied changes from stencil testing. Fixed some packages. Altered functional groups. Other Misc. Changes. This is immediately before component mass renaming.
    [Baseplate.stl, VARA.brd, VARB.brd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]
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2021-01-18 Cleaned up various minor silkscreen issues
    [evpr.brd, evpr.sch]
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2021-01-18 Negative using signals correctly marked as negative
    [evpr.brd, evpr.sch]
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2021-01-18 Created OSH version with out-of-board holes removed and shims added. Bumped revision to MKII.D
    [evpr.brd, evpr_osh.brd, evpr_osh.sch]
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2021-01-19 Performed DRC checks, fixed minor issues, redid OSH version
    [evpr.brd, evpr.sch, evpr_osh.brd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]
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2021-02-06 electronics - made tooling dir, moved paster to there
    [paster.stl]
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2021-07-10 Rectify ESP32 land pattern, increase margin between vias under ESP32 and its contacts, increase exposure area for pads of C.DS1
    [evpr.brd, evpr.sch]
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2021-07-16 Remove USB interface from EVPR, design external programmer board
    [ESP32_USB_INTERFACE_NOESP.brd, ESP32_USB_INTERFACE_NOESP.sch, evpr.brd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]
2021-07-16 Update mainboard and progboard to use smaller connector
    [ESP32_USB_INTERFACE_NOESP.brd, ESP32_USB_INTERFACE_NOESP.sch, evpr.brd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]
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2021-08-19 Add BOM with pricechecks for EVPR revD card (using RevC part codes)
    [EVPR RevD BOM with RevC codes.ods]
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2021-08-29 Silkscreen adjustments, some DRC issues adjustments
    [evpr.brd, evpr.sch, evpr_osh.brd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]
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2021-08-29 Fix GND label
    [EVPR Brush.brd]
2021-08-29 Fix label alignment
    [EVPR Brush.brd]
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2021-09-02 brushes - deleted copper plate data no longer needed
    [copper_plate.ods]
2021-09-02 brushes - moved brush holder assembly and files under hardware
    [brush_design.ods, brush_holder_mm.curaproject.3mf, brush_holder_mm.stl]
2021-09-17 rotor blade - added tooling for ccw blade
    [mold_box.ods]
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2021-09-17 plate - moved tooling files to separate dir
    [plate_one_in.stl, plate_two_in.stl]
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2021-09-26 hardware, plate tooling - updated tooling info for plate one
    [plate_one_in.stl]
2021-09-26 hardware, plate - updated CAD to be consistent with plate one, added short description
    [plate_two_in.stl]
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2021-10-16 brush holder - updated for new brush contacts and addition of magnets
    [brush_holder_mm.3mf, brush_holder_mm.curaproject.3mf, brush_holder_mm.stl]
2021-10-17 brush_plates - added in house variations back into master with some tweaks
    [brush_plate_ground_in.stl, brush_plate_power_in.stl, copper_plate.ods]
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2021-10-27 broke out subassemblies for rotor hub
2021-11-16 hub - removed old assembly which had bugs, made hub common
2021-11-16 misc - added subassemblies and other parts for hub
    [92510A018_unthreaded_spacer.stp]
2021-11-17 misc - added shaft and pully subassemblies, new evpr_ccw subassembly
    [2780T43.STEP, 5947K150.STEP, 96363A578.STEP]
2021-11-21 plate two - fixed tool paths to address machinining issues for 6-32 threaded holes
